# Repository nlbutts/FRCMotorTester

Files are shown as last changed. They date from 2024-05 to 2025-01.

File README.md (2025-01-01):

# Brushless Buddy
This is a small PCB with a display and two rotary encoders. The device
is designed to help teams quickly prototype BLC designs using the Rev SparkMax
motor controllers. Although it could be expanded to support other devices.

# Design
The block diagram is shown below. The design consists of an input buck regulator.
The regulator should be good up to 24V, but was designed to work at 12V. There
is reverse battery protection, so it should handle accidentially connecting
the battery up in reverse.

The buck generates 5V which is used for the CAN transceiver. The 5V is fed
to two LDO's to generate 3.3V for the processor and 3.0V for the LCD backlight.

There are two status LEDs on the board, two rotary encoders, and a 128x32 pixel
graphical LCD. An STM32F446 processor powers everything.

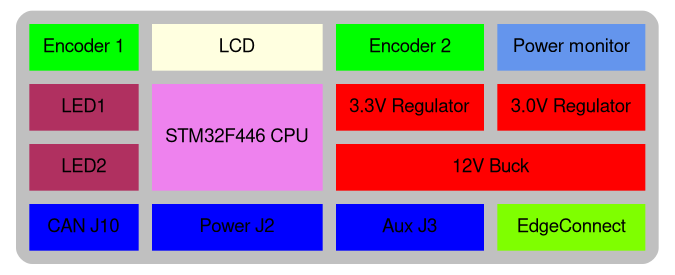
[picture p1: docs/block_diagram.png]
block diagram


There are three user accessible connectors:
Power J2:
| Pin | Use |
| -- | -- |
| 1 | Ground |
| 2 | Power |

The mate is a **JST PHR-2**

CAN J10:
| Pin | Use |
| -- | -- |
| 1 | CAN High |
| 2 | CAN Low |
| 3 | CAN High |
| 4 | CAN Low |

The pinout is the same as the Spark MAX and uses the same connector.
The mate is a **JST PHR-4**

Aux J3:
| Pin | Use |
| -- | -- |
| 1 | 3.3V |
| 2 | Ground |
| 3 | GPIO1 |
| 4 | GPIO2 |
| 5 | GPIO3 |
| 6 | Analog Input |

The mate is a **JST PHR-6**
The auxiliary connector is used for future use cases. It just made sense to
throw this connector on.

The picture below shows the location of the connectors.
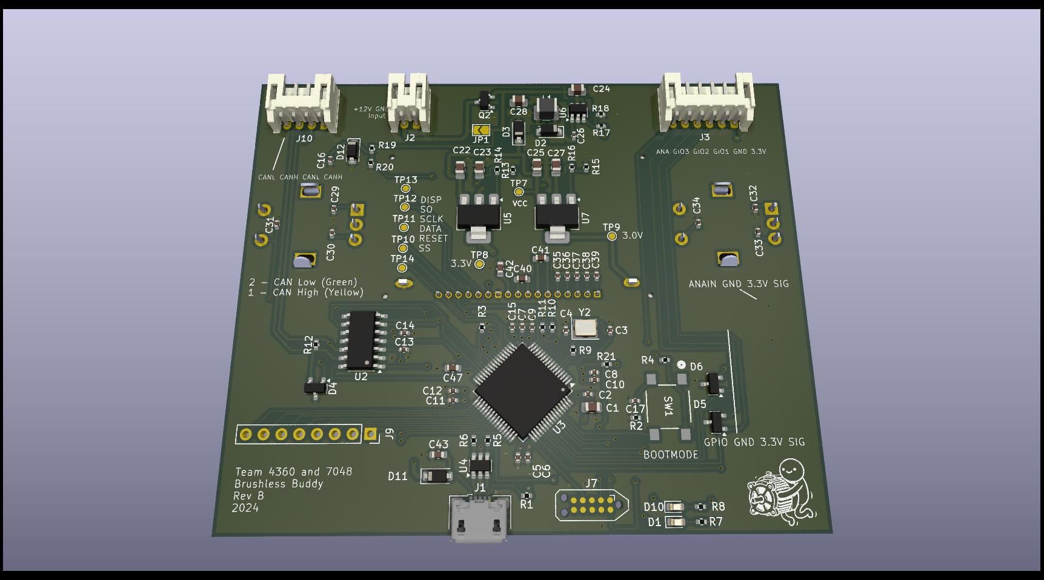
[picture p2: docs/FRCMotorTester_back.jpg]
connectors


# Software
The design runs Micropython. To re-build the code do the following:
1) Download the ARM GCC compiler [GCC](https://developer.arm.com/-/media/Files/downloads/gnu/13.3.rel1/binrel/arm-gnu-toolchain-13.3.rel1-x86_64-arm-none-eabi.tar.xz)
2) Decompress the toolchain to some known location, we will call this *<gcc_emd>*
3) Open a command prompt and update your path: `export PATH=<gcc_emd>/bin:$PATH`
4) Check out this repo, we will call this directory *<repo>*
5) Navigate to *<repo>/software/micropython
6) `make -C mpy-cross -j`
7) `BOARD=FRCMOTOR make -C ports/stm32/ -j`
8) Connect the Tagconnect to the board.
9) Program **firmware.elf** using the STM32CubeProgrammer.

## SWD Debug
It is assumed you are using a JLink and it is installed in **/opt/SEGGER/JLink**
In the software directory:
1) Run **gdbstart.sh** in one terminal
2) Run debug.sh in other terminal. You now have the full power of GDB at your literial finger tips

## Python

This device runs micropython. So the main program is a Python program. The
main program is called **main.py**, catchy aint it?

There are two levels of software upgrades. If you need to upgrade the Python code,
simply update main.py and copy it over to the **PYBFLASH** device.

If you need to update Micropython, then use a terminal program to open the REPL terminal.
Hit CTRL-C to stop the program. Then type
```
import machine
machine.bootloader()
```

This will put the processor in DFU upgrade mode. You can now use STM32CubeProgrammer to program
the DFU file. If the upgrade fails, then the device will have to be JTAGed. The next rev
of the PCB will fix a defect and a physical button will allow the unit to be booted in DFU mode.

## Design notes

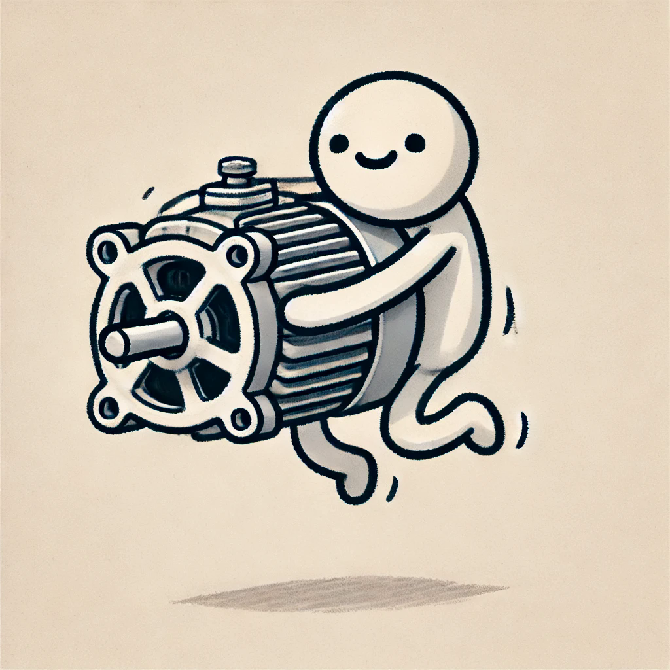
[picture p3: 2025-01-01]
brushless_buddy.png

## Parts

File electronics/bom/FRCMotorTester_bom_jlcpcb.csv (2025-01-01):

Designator | Comment | Footprint | JLCPCB
C1 | 4.7u | Capacitor_SMD:C_0805_2012Metric | C1779
C2 | 0.1u | Capacitor_SMD:C_0402_1005Metric | C1525
C3 | 15p | Capacitor_SMD:C_0402_1005Metric | C1548
C4 | 15p | Capacitor_SMD:C_0402_1005Metric | C1548
C5 | 0.1u | Capacitor_SMD:C_0402_1005Metric | C1525
C6 | 0.1u | Capacitor_SMD:C_0402_1005Metric | C1525
C7 | 0.1u | Capacitor_SMD:C_0402_1005Metric | C1525
C8 | 0.1u | Capacitor_SMD:C_0402_1005Metric | C1525
C9 | 0.1u | Capacitor_SMD:C_0402_1005Metric | C1525
C10 | 0.1u | Capacitor_SMD:C_0402_1005Metric | C1525
C11 | 0.1u | Capacitor_SMD:C_0402_1005Metric | C1525
C12 | 0.1u | Capacitor_SMD:C_0402_1005Metric | C1525
C13 | 0.1u | Capacitor_SMD:C_0402_1005Metric | C1525
C14 | 0.1u | Capacitor_SMD:C_0402_1005Metric | C1525
C15 | 1u | Capacitor_SMD:C_0402_1005Metric | C52923
C16 | 1u | Capacitor_SMD:C_0402_1005Metric | C52923
C17 | 0.1u | Capacitor_SMD:C_0402_1005Metric | C1525
C22 | 10u | Capacitor_SMD:C_0805_2012Metric | C15850
C23 | 10u | Capacitor_SMD:C_0805_2012Metric | C15850
C24 | 10u | Capacitor_SMD:C_0805_2012Metric | C15850
C25 | 10u | Capacitor_SMD:C_0805_2012Metric | C15850
C26 | 10n | Capacitor_SMD:C_0402_1005Metric | C15195
C27 | 10u | Capacitor_SMD:C_0805_2012Metric | C15850
C28 | 10u | Capacitor_SMD:C_0805_2012Metric | C15850
C29 | 10n | Capacitor_SMD:C_0402_1005Metric | C15195
C30 | 10n | Capacitor_SMD:C_0402_1005Metric | C15195
C31 | 0.1u | Capacitor_SMD:C_0402_1005Metric | C1525
C32 | 10n | Capacitor_SMD:C_0402_1005Metric | C15195
C33 | 10n | Capacitor_SMD:C_0402_1005Metric | C15195
C34 | 0.1u | Capacitor_SMD:C_0402_1005Metric | C1525
C35 | 1u | Capacitor_SMD:C_0402_1005Metric | C52923
C36 | 1u | Capacitor_SMD:C_0402_1005Metric | C52923
C37 | 1u | Capacitor_SMD:C_0402_1005Metric | C52923
C38 | 1u | Capacitor_SMD:C_0402_1005Metric | C52923
C39 | 1u | Capacitor_SMD:C_0402_1005Metric | C52923
C40 | 2.2u | Capacitor_SMD:C_0603_1608Metric | C23630
C41 | 2.2u | Capacitor_SMD:C_0603_1608Metric | C23630
C42 | 2.2u | Capacitor_SMD:C_0603_1608Metric | C23630
C43 | 2.2u | Capacitor_SMD:C_0603_1608Metric | C23630
C47 | 2.2u | Capacitor_SMD:C_0603_1608Metric | C23630
D1 | LED | LED_SMD:LED_0603_1608Metric | C2286
D2 | D_Schottky | Diode_SMD:D_SOD-123 | C8598
D3 | D_Schottky | Diode_SMD:D_SOD-123 | C8598
D4 | SP0502BAHT | Package_TO_SOT_SMD:SOT-23 | C32677
D5 | SP0502BAHT | Package_TO_SOT_SMD:SOT-23 | C32677
D6 | SP0502BAHT | Package_TO_SOT_SMD:SOT-23 | C32677
D10 | LED | LED_SMD:LED_0603_1608Metric | C2286
D11 | D_Schottky | Diode_SMD:D_SOD-123 | C8598
D12 | D_Zener | Diode_SMD:D_SOD-123 | C2105
DS1 | NHD-C12832A1Z-FSW-FBW-3V3 | footprints:LCD_NHD-C12832A1Z-FSW-FBW-3V3
J1 | USB_B_Micro | Connector_USB:USB_Micro-B_Amphenol_10118193-0001LF_Horizontal | C132562
J2 | Conn_01x02_Socket | Connector_JST:JST_PH_S2B-PH-K_1x02_P2.00mm_Horizontal | C173752
J3 | Conn_01x06 | Connector_JST:JST_PH_S6B-PH-K_1x06_P2.00mm_Horizontal | C471518
J10 | Conn_01x04 | Connector_JST:JST_PH_S4B-PH-K_1x04_P2.00mm_Horizontal | C160354
L1 | L | Inductor_SMD:L_1210_3225Metric | C1330201
Q2 | IRLML6401 | Package_TO_SOT_SMD:SOT-23 | C2593
R1 | 560 | Resistor_SMD:R_0402_1005Metric | C25126
R2 | 100k | Resistor_SMD:R_0402_1005Metric | C102750
R3 | 100k | Resistor_SMD:R_0402_1005Metric | C102750
R4 | 1K | Resistor_SMD:R_0402_1005Metric | C11702
R5 | 22 | Resistor_SMD:R_0402_1005Metric | C25152
R6 | 22 | Resistor_SMD:R_0402_1005Metric | C25152
R7 | 330 | Resistor_SMD:R_0402_1005Metric | C12246
R8 | 330 | Resistor_SMD:R_0402_1005Metric | C12246
R9 | 1K | Resistor_SMD:R_0402_1005Metric | C11702
R10 | 20k | Resistor_SMD:R_0402_1005Metric | C93942
R11 | 10k | Resistor_SMD:R_0402_1005Metric | C25744
R12 | 120 | Resistor_SMD:R_0402_1005Metric | C25079
R13 | 1.6k | Resistor_SMD:R_0402_1005Metric | C102825
R14 | 1k | Resistor_SMD:R_0402_1005Metric | C11702
R15 | 1.3k | Resistor_SMD:R_0402_1005Metric | C4906
R16 | 1k | Resistor_SMD:R_0402_1005Metric | C11702
R17 | 49.9k | Resistor_SMD:R_0402_1005Metric | C100457
R18 | 9.53k | Resistor_SMD:R_0402_1005Metric | C103191
R19 | 100k | Resistor_SMD:R_0402_1005Metric | C102750
R20 | 10k | Resistor_SMD:R_0402_1005Metric | C25744
R21 | 4.7k | Resistor_SMD:R_0402_1005Metric | C103059
SW1 | PTS645SK50SMTR92LFS | footprints:PTS645SK50SMTR92LFS_CNK | C221872
U2 | TCAN1043xDxQ1 | Package_SO:SOIC-14_3.9x8.7mm_P1.27mm | C1848115
U3 | STM32F446RETx | Package_QFP:LQFP-64_10x10mm_P0.5mm | C69336
U4 | USBLC6-2SC6 | Package_TO_SOT_SMD:SOT-23-6 | C7519
U5 | LM1117DT-ADJ | Package_TO_SOT_SMD:SOT-223-3_TabPin2 | C2902259
U6 | AOZ1280CI | Package_TO_SOT_SMD:SOT-23-6 | C41240
U7 | LM1117DT-ADJ | Package_TO_SOT_SMD:SOT-223-3_TabPin2 | C2902259
Y2 | Crystal_GND24 | Crystal:Crystal_SMD_3225-4Pin_3.2x2.5mm | C156247

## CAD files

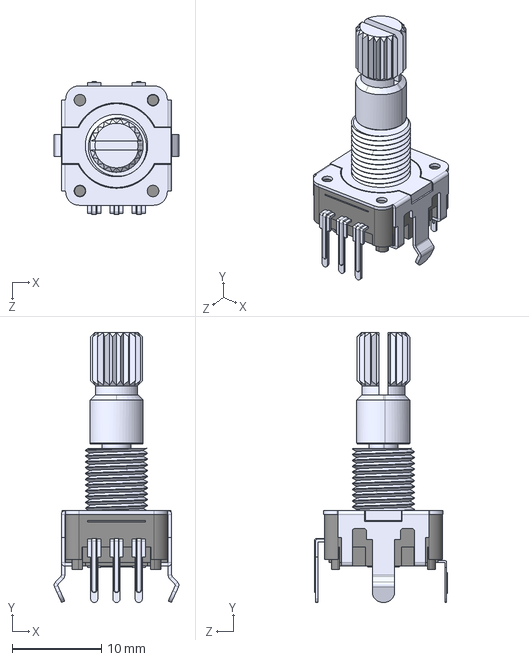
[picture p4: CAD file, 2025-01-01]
mechanical/PEC11R-4220K-S0024.STEP
14.0 x 30.3 x 14.9 mm

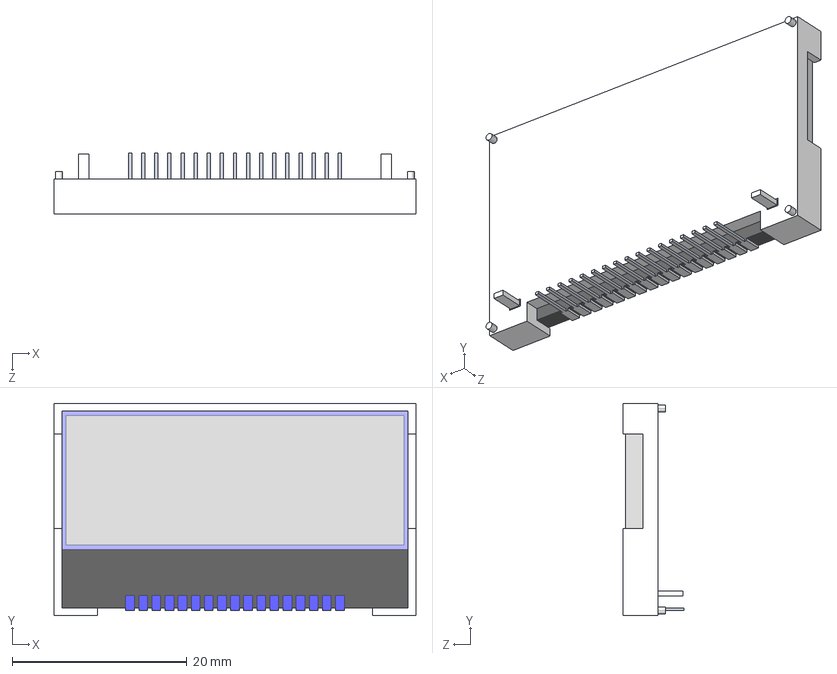
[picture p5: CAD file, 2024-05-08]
mechanical/NHD-C12832A1Z.STEP
41.4 x 24.3 x 7.00 mm

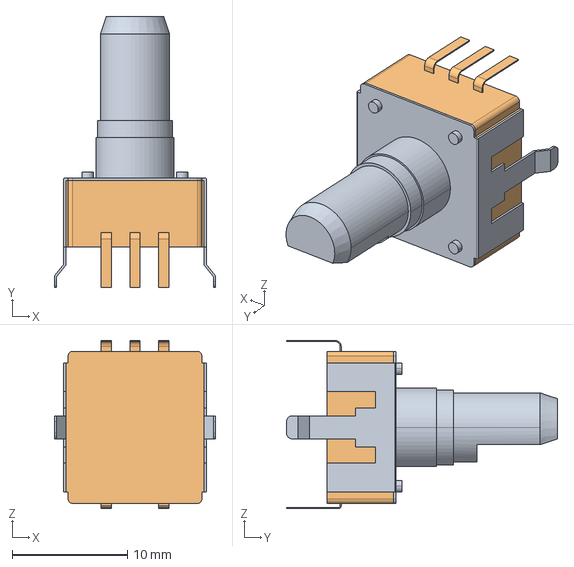
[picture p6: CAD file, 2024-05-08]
mechanical/en12-hs22af20.stp
14.0 x 23.5 x 14.6 mm
BM-427
BM-428

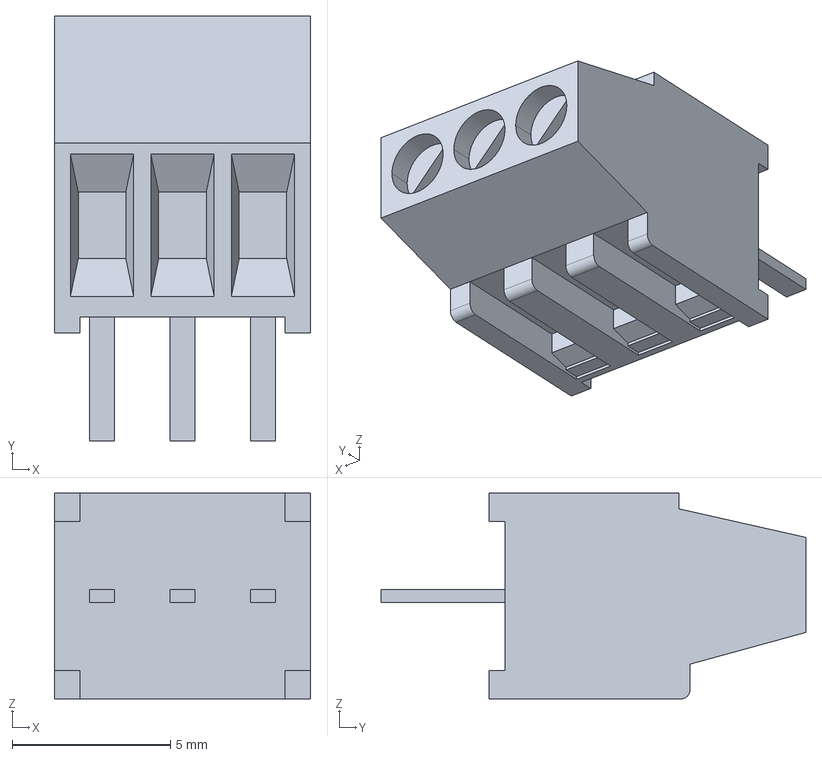
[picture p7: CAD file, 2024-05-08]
mechanical/c-282834-3-c-3d.stp
8.08 x 13.4 x 6.50 mm

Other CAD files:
mechanical/FRCMotorTester.step
mechanical/W25Q32JVZPIQ.step
mechanical/PTS645SK50SMTR92LFS.step
mechanical/LQH3NPN4R7MMEL.step
mechanical/CUI_DEVICES_TS04-66-65-BK-260-SMT.step
mechanical/CUI_DEVICES_TB002-500-02BE.step
mechanical/QFN28_6X6MC_MCH.step

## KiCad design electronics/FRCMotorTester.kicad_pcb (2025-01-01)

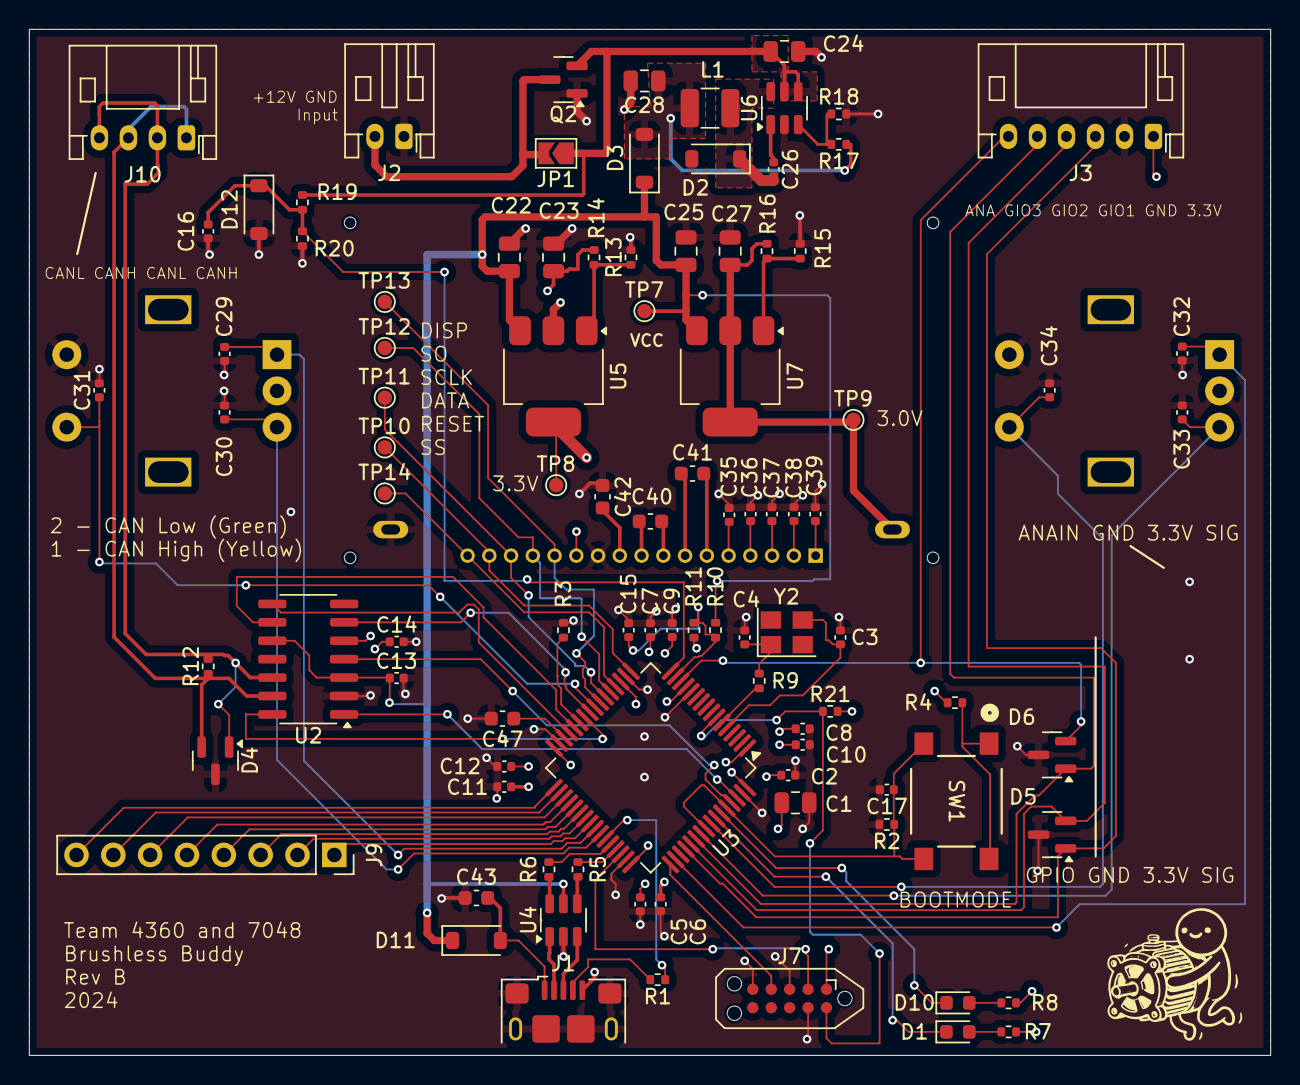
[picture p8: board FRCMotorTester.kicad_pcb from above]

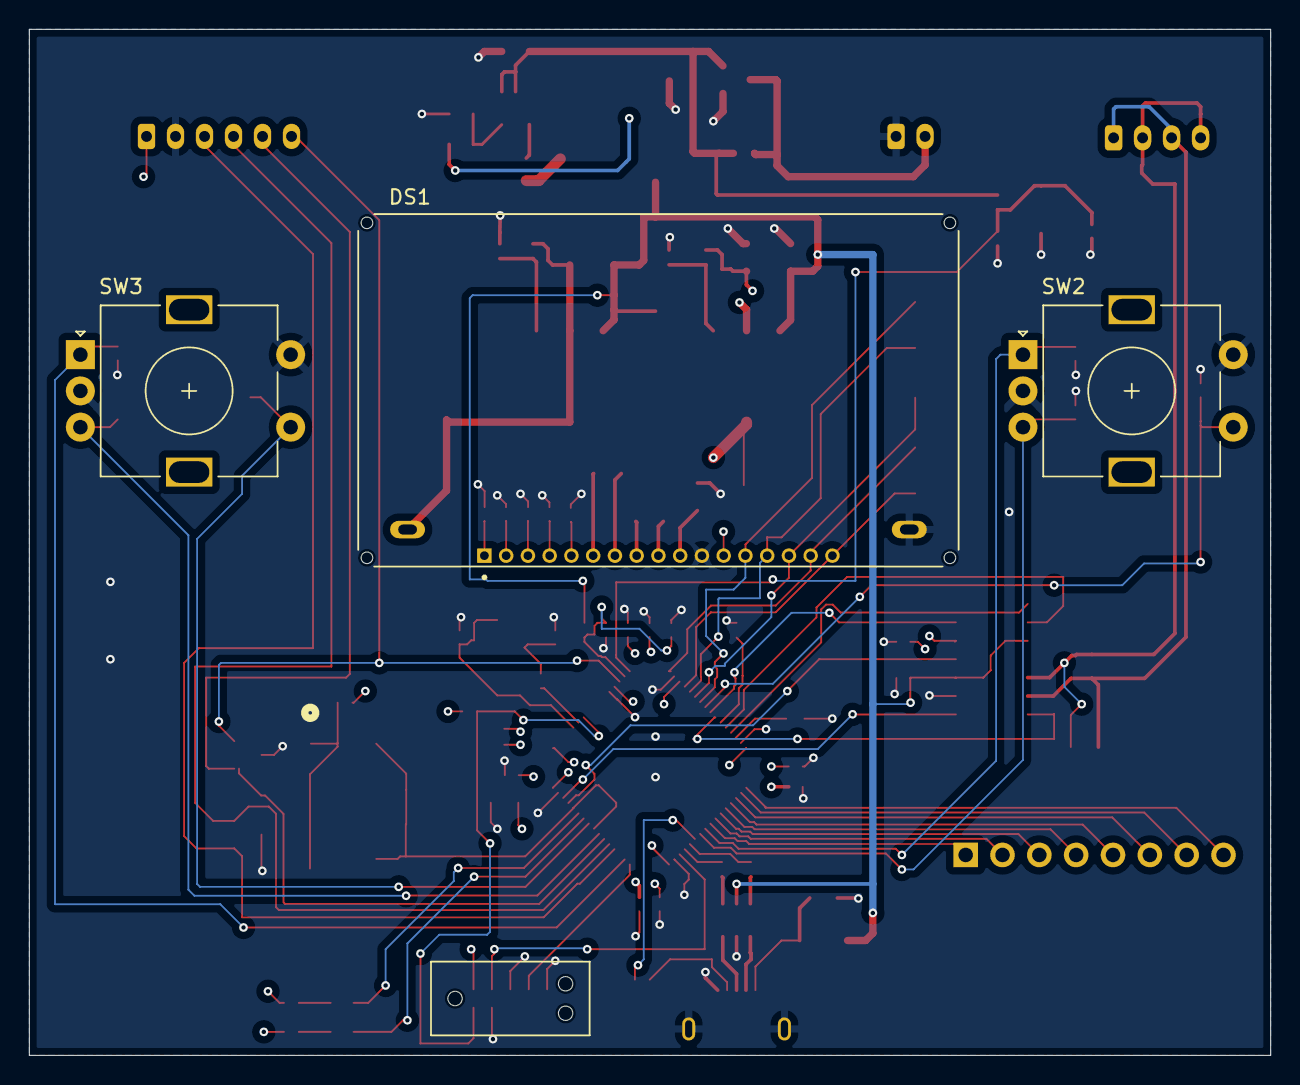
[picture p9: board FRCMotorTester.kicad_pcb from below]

Board: 4 copper layers, 85.6 x 70.8 mm, 99 parts (3 on the bottom side), 78 nets.

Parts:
C1: 4.7u; C_0805_2012Metric
C2, C5, C6, C7, C8, C9, C10, C11, C12, C13, C14, C17, C31, C34: 0.1u; C_0402_1005Metric
C3, C4: 15p; C_0402_1005Metric
C15, C16, C35, C36, C37, C38, C39: 1u; C_0402_1005Metric
C22, C23, C24, C25, C27, C28: 10u; C_0805_2012Metric
C26, C29, C30, C32, C33: 10n; C_0402_1005Metric
C40, C41, C42, C43, C47: 2.2u; C_0603_1608Metric
D1, D10: LED; LED_0603_1608Metric
D2, D3, D11: D_Schottky; D_SOD-123
D4, D5, D6: SP0502BAHT; SOT-23
D12: D_Zener; D_SOD-123
DS1: NHD-C12832A1Z-FSW-FBW-3V3; LCD_NHD-C12832A1Z-FSW-FBW-3V3
H1: MountingHole; brushless_buddy_logo
J1: USB_B_Micro; USB_Micro-B_Amphenol_10118193-0001LF_Horizontal
J2: Conn_01x02_Socket; JST_PH_S2B-PH-K_1x02_P2.00mm_Horizontal
J3: Conn_01x06; JST_PH_S6B-PH-K_1x06_P2.00mm_Horizontal
J7: Conn_ARM_JTAG_SWD_10; Tag-Connect_TC2050-IDC-NL_2x05_P1.27mm_Vertical_with_bottom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
J9: Conn_01x08; PinSocket_1x08_P2.54mm_Vertical
J10: Conn_01x04; JST_PH_S4B-PH-K_1x04_P2.00mm_Horizontal
JP1: Jumper_NO_Small; SolderJumper-2_P1.3mm_Open_TrianglePad1.0x1.5mm
L1: L; L_1210_3225Metric
Q2: IRLML6401; SOT-23
R1: 560; R_0402_1005Metric
R2, R3, R19: 100k; R_0402_1005Metric
R4, R9: 1K; R_0402_1005Metric
R5, R6: 22; R_0402_1005Metric
R7, R8: 330; R_0402_1005Metric
R10: 20k; R_0402_1005Metric
R11, R20: 10k; R_0402_1005Metric
R12: 120; R_0402_1005Metric
R13: 1.6k; R_0402_1005Metric
R14, R16: 1k; R_0402_1005Metric
R15: 1.3k; R_0402_1005Metric
R17: 49.9k; R_0402_1005Metric
R18: 9.53k; R_0402_1005Metric
R21: 4.7k; R_0402_1005Metric
SW1: PTS645SK50SMTR92LFS; PTS645SK50SMTR92LFS_CNK
SW2, SW3: RotaryEncoder_Switch; RotaryEncoder_Alps_EC11E-Switch_Vertical_H20mm
TP7, TP8, TP9, TP10, TP11, TP12, TP13, TP14: TestPoint; TestPoint_Pad_D1.0mm
U2: TCAN1043xDxQ1; SOIC-14_3.9x8.7mm_P1.27mm
U3: STM32F446RETx; LQFP-64_10x10mm_P0.5mm
U4: USBLC6-2SC6; SOT-23-6
U5, U7: LM1117DT-ADJ; SOT-223-3_TabPin2
U6: AOZ1280CI; SOT-23-6
Y2: Crystal_GND24; Crystal_SMD_3225-4Pin_3.2x2.5mm

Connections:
3V0: C27.1, DS1.A (LED+), R16.1, TP9.1, U7.2 (VO)
3V3: C1.1, C2.1, C5.1, C6.1, C7.1, C8.1, C9.1, C10.1, C11.1, C12.1, C14.1, C23.1, DS1.12 (VDD), J3.1, J7.1 (VTref), R4.1, R7.2, R8.2, R14.1, R21.2, TP8.1, U2.5 (VIO), U3.1 (VBAT), U3.13 (VDDA), U3.19 (VDD), U3.32 (VDD), U3.48 (VDD), U3.64 (VDD), U5.2 (VO)
+12V: C24.1, JP1.1, Q2.2 (S), R19.1, U6.4 (EN), U6.5 (VIN)
/Pico/OSC_IN: C3.2, U3.5 (PH0), Y2.3
/Pico/OSC_OUT: C4.2, R9.2, Y2.1
/Power/VIN: J2.2, JP1.2, Q2.3 (D)
ANALOG_IN: D6.2 (K), J3.6, U3.14 (PA0)
BOOT: C17.1, R2.1, SW1.3, SW1.4, U3.56 (PB4), U3.60 (BOOT0)
CAN_EN: U2.6 (EN), U3.25 (PC5)
CAN_FAULT: U2.8 (~FAULT), U3.29 (PB10)
CAN_RX: U2.4 (RXD), U3.61 (PB8)
CAN_STB: U2.14 (~STB), U3.26 (PB0)
CAN_TX: U2.1 (TXD), U3.62 (PB9)
CAN_WAKE: U2.9 (WAKE), U3.28 (PB2)
DISP_DATA: DS1.15 (A0), TP11.1, U3.22 (PA6)
DISP_RESET: DS1.16 (~RST), TP10.1, U3.17 (PA3)
DISP_SCLK: DS1.14 (SCL), TP12.1, U3.21 (PA5)
DISP_SI: DS1.13 (SI), TP13.1, U3.23 (PA7)
DISP_SS: DS1.17 (~CS1), TP14.1, U3.20 (PA4)
DM: R6.2, U3.44 (PA11)
DP: R5.2, U3.45 (PA12)
ENC1A: C29.1, SW2.A, U3.41 (PA8)
ENC1B: C30.1, SW2.B, U3.42 (PA9)
ENC2A: C32.1, SW3.A, U3.50 (PA15)
ENC2B: C33.1, SW3.B, U3.55 (PB3)
GENIO_01: D5.1 (K), J3.3, U3.52 (PC11)
GENIO_02: D5.2 (K), J3.4, U3.53 (PC12)
GENIO_03: D6.1 (K), J3.5, U3.54 (PD2)
GND: C1.2, C2.2, C3.1, C4.1, C5.2, C6.2, C7.2, C8.2, C9.2, C10.2, C11.2, C12.2, C13.2, C14.2, C15.2, C16.2, C17.2, C22.2, C23.2, C24.2, C25.2, C27.2, C28.2, C29.2, C30.2, C31.2, C32.2, C33.2, C34.2, C35.1, C36.1, C37.1, C38.1, C39.1, C42.1, C43.1, C47.2, D2.2 (A), D4.3 (A), D5.3 (A), D6.3 (A), D12.2 (A), DS1.11 (VSS), DS1.K (LED-), J1.5 (GND), J1.6 (Shield), J2.1, J3.2, J7.3 (GND), J7.5 (GND), J7.9 (GNDDetect), Q2.1 (G), R2.2, R3.2, R11.2, R13.2, R15.2, R18.2, R20.2, SW2.C, SW2.S2, SW3.C, SW3.S2, U2.2 (GND), U3.12 (VSSA), U3.18 (VSS), U3.31 (VSS), U3.47 (VSS), U3.63 (VSS), U4.2 (GND), U6.2 (GND)
ID: R1.1, U3.43 (PA10)
LED1: D1.1 (K), U3.58 (PB6)
LED2: D10.1 (K), U3.59 (PB7)
NRST: J7.10 (~RESET), R21.1, U3.7 (NRST)
unnamed: D1.2 (A), R7.1
unnamed: C26.2, D2.1 (K), L1.1, U6.6 (LX)
unnamed: C28.1, D3.2 (A), L1.2, R17.1
unnamed: D10.2 (A), R8.1
unnamed: C43.2, D11.2 (A), J1.1 (VBUS)
unnamed: C40.1, DS1.8 (C1+)
unnamed: C40.2, DS1.9 (C1-)
unnamed: C41.1, DS1.7 (C2+)
unnamed: C41.2, DS1.6 (C2-)
unnamed: C39.2, DS1.1 (V0)
unnamed: C38.2, DS1.2 (V1)
unnamed: C37.2, DS1.3 (V2)
unnamed: C36.2, DS1.4 (V3)
unnamed: C35.2, DS1.5 (V4)
unnamed: C42.2, DS1.10 (VOUT)
unnamed: J1.3 (D+), U4.3 (I/O2)
unnamed: J1.2 (D-), U4.1 (I/O1)
unnamed: J1.4 (ID), R1.2
unnamed: D4.2 (K), J10.1, J10.3, R12.1, U2.13 (CANH)
unnamed: D4.1 (K), J10.2, J10.4, R12.2, U2.12 (CANL)
unnamed: R4.2, SW1.1, SW1.2
unnamed: R5.1, U4.4 (I/O2)
unnamed: R6.1, U4.6 (I/O1)
unnamed: R3.1, U3.27 (PB1)
unnamed: R9.1, U3.6 (PH1)
unnamed: C47.1, U3.30 (VCAP_1)
unnamed: R13.1, R14.2, U5.1 (ADJ)
unnamed: C26.1, U6.1 (BST)
unnamed: R17.2, R18.1, U6.3 (FB)
unnamed: R15.1, R16.2, U7.1 (ADJ)
PRESS1: C31.1, SW2.S1, U3.24 (PC4)
PRESS2: C34.1, SW3.S1, U3.57 (PB5)
SPARE1: J9.1, U3.40 (PC9)
SPARE2: J9.2, U3.39 (PC8)
SPARE3: J9.3, U3.38 (PC7)
SPARE4: J9.4, U3.37 (PC6)
SPARE5: J9.5, U3.36 (PB15)
SPARE6: J9.6, U3.35 (PB14)
SPARE7: J9.7, U3.34 (PB13)
SPARE8: J9.8, U3.33 (PB12)
SWCLK: J7.4 (SWCLK/TCK), U3.49 (PA14)
SWDIO: J7.2 (SWDIO/TMS), U3.46 (PA13)
VCC: C13.1, C22.1, C25.1, D3.1 (K), D11.1 (K), R10.1, TP7.1, U2.3 (VCC), U2.10 (VSUP), U4.5 (VBUS), U5.3 (VI), U7.3 (VI)
VCC_MEAS: C15.1, R10.2, R11.1, U3.15 (PA1)
VIN_MEAS: C16.1, D12.1 (K), R19.2, R20.1, U3.16 (PA2)

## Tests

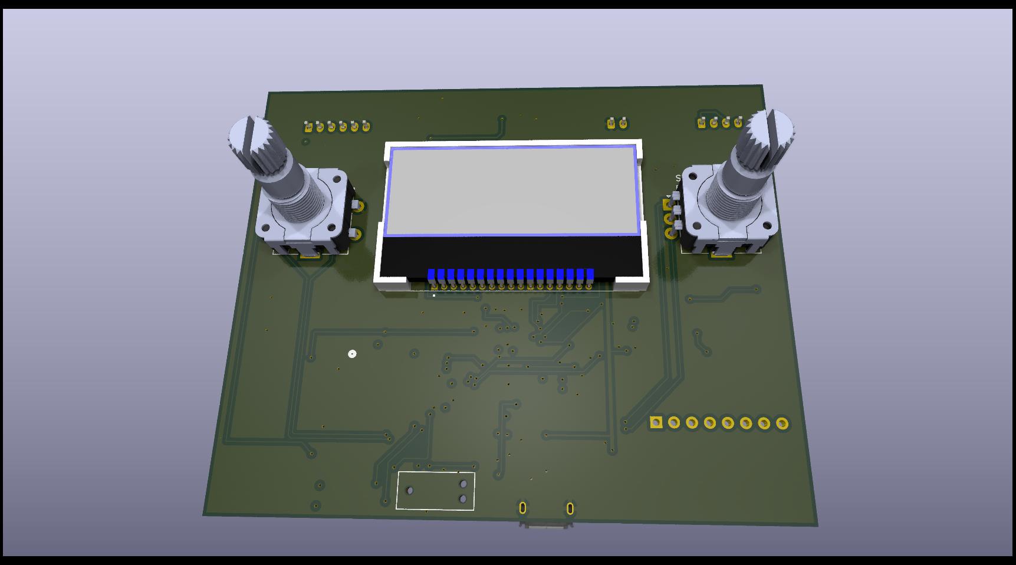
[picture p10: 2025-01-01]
docs/FRCMotorTester_front.jpg

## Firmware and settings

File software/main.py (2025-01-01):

from machine import Pin
from pyb import CAN
import pyb
import time
import sys
import struct

VERSION = 1.0

class SparkMax():
    def __init__(self, can, id, enc):
        self.can = can
        self.id = id
        self.enc = enc
        self.prev_button = 1
        self.arm = False
        self.volts = 0
        self.current = 0
        self.motor_output = 0.0
        self.enc.set_counter(0)

    def make_filter(self, class_idx):
        """Make a message filter

        Args:
            class_idx (int): combination of the API class and index
        """
        devtype = 2
        mfg = 5
        can_id = devtype << 24 | mfg << 16 | class_idx << 6 | self.id
        return can_id

    def process_button(self):
        button = self.enc.get_press()
        if not button and self.prev_button:
            self.arm = not self.arm
            if not self.arm:
                self.enc.set_counter(0)

        self.prev_button = button

    def process(self, msg):
        self.process_button()

        can_id = msg[0]
        dev = can_id & 0x3F
        api = (can_id >> 6) & 0x3FF
        if dev == self.id:
            if api == 0x61:
                data = msg[4]
                volts = ((data[6] & 0x0F) << 8) | data[5]
                self.volts = volts / 128.0
                current = data[7] << 4 | (data[6] >> 4) & 0xF
                self.current = current / 20

        if self.enc.get_counter() > 100:
            self.enc.set_counter(100)
        elif self.enc.get_counter() < -100:
            self.enc.set_counter(-100)
        self.motor_output = -(self.enc.get_counter())
        self.motor_output /= 100
        self.drive_motor(self.motor_output)

    def get_arm_str(self):
        if self.arm:
            return 'ARMD'
        return 'SAFE'

    def get_info(self):
        info = {}
        info['id'] = self.id
        info['arm'] = self.get_arm_str()
        info['volt'] = self.volts
        info['current'] = self.current
        info['output'] = self.motor_output
        return info

    def drive_motor(self, output):
        """
        Driving motor 2 uses this message: DevID: 0 idx: 2 cls: 11 mfg: 5 devtype: 2 raw: 02052C80 data: 04 00 00 00 00 00 00 00
        At -0.12 DevID: 2 idx: 2 cls: 0 mfg: 5 devtype: 2 raw: 02050082 data: 8F C2 F5 BD 00 00 00 00
        Driving motor 4 uses this message: DevID: 0 idx: 2 cls: 11 mfg: 5 devtype: 2 raw: 02052C80 data: 10 00 00 00 00 00 00 00
        """
        if self.arm:
            devtype = 2
            mfg = 5
            cls = 0
            idx = 2
            can_id = devtype << 24 | mfg << 16 | cls << 10 | idx << 6 | self.id
            data = struct.pack('<fBBBB', output, 0, 0, 0, 0)  # Format the payload
            self.can.send(data, can_id, extframe=True)  # Send the CAN message

    def debug_can(self, message):
        """Debug the can message

        Args:
            message (_type_): _description_
        """
        id = message[0]
        devtype = id >> 24
        mfg = (id >> 16) & 0xFF
        cls = (id >> 10) & 0x3F
        idx = (id >> 6) & 0xF
        devid = id & 0x3F
        s = f'DevID: {devid} idx: {idx} cls: {cls} mfg: {mfg} devtype: {devtype} raw: {id:08X} data: '
        for b in message[4]:
            s += f'{b:02X} '
        print(s)

def get_spark_max_ids(can, delay=2):
    try:
        ids = {}
        start = time.time()
        while time.time() - start < delay:
            m = can.recv(0)
            id = m[0] & 0x3F
            if id > 0:
                ids[id] = 1
        print(ids)
        return list(ids.keys())
    except:
        return []

class Encoder():
    def __init__(self, enc_name):
        if 'Left' in enc_name:
            self.pin_a = Pin('ENC2A', Pin.AF_PP, pull=Pin.PULL_UP, af=Pin.AF1_TIM2)
            self.pin_b = Pin('ENC2B', Pin.AF_PP, pull=Pin.PULL_UP, af=Pin.AF1_TIM2)
            self.press = Pin('PRESS2', Pin.IN, pull=Pin.PULL_UP)
            self.tim = pyb.Timer(2, prescaler=0, period=100)
            self.ch = self.tim.channel(1, pyb.Timer.ENC_AB)
        elif 'Right' in enc_name:
            self.pin_a = Pin('ENC1A', Pin.AF_PP, pull=Pin.PULL_UP, af=Pin.AF1_TIM1)
            self.pin_b = Pin('ENC1B', Pin.AF_PP, pull=Pin.PULL_UP, af=Pin.AF1_TIM1)
            self.press = Pin('PRESS1', Pin.IN, pull=Pin.PULL_UP)
            self.tim = pyb.Timer(1, prescaler=0, period=100)
            self.ch = self.tim.channel(1, pyb.Timer.ENC_AB)

    def get_press(self):
        return self.press.value()

    def get_counter(self):
        return self.tim.counter() - 500

    def set_counter(self, value):
        self.tim.counter(500 + value)

sw = Pin('SW', Pin.IN)
prev = sw.value()

lcd = pyb.LCD('X')

can_txd = Pin('CAN_TX', Pin.AF_PP, af=Pin.AF9_CAN1)
can_rxd = Pin('CAN_RX', Pin.AF_PP, af=Pin.AF9_CAN1)

can_en = Pin('CAN_EN', Pin.OUT)
can_fault = Pin('CAN_FAULT', Pin.IN)
can_wake = Pin('CAN_WAKE', Pin.OUT)
can_stb = Pin('CAN_STB', Pin.OUT)

can_en.value(1)
can_fault.value(1)
can_wake.value(1)
can_stb.value(1)

# Initialize CAN bus
can = CAN(1, CAN.NORMAL)

# Configure the CAN bus settings
can.init(CAN.NORMAL, prescaler=2, sjw=1, bs1=14, bs2=6, auto_restart=True)
can.setfilter(0, can.MASK32, 0, (0, 0), extframe=True)
can.send('hello', 0, extframe=True)

leftEnc = Encoder('Left')
rightEnc = Encoder('Right')

def show_boot_screen(can_ids=[]):
    lcd.fill(0)
    lcd.text(f'Brushless Buddy', 0, 0, 1)
    lcd.text(f'Ver: {VERSION}', 0, 10, 1)
    if len(can_ids) > 0:
        s = 'Found: '
        for id in can_ids:
            s += f'{id} '
        lcd.text(s, 0, 20, 1)
    else:
        lcd.text(f'Found: None', 0, 20, 1)
    lcd.show()

show_boot_screen()
ids = sorted(get_spark_max_ids(can))
print(f'Found ids: {ids}')

if len(ids) > 2:
    lcd.fill(0)
    lcd.text('Too many CAN', 0, 0, 1)
    lcd.text('nodes on bus', 0, 10, 1)
    lcd.show()
    time.sleep(5)
    sys.reset()
if len(ids) == 0:
    lcd.fill(0)
    lcd.text('No SparkMaxs', 0, 0, 1)
    lcd.text('detected', 0, 10, 1)
    lcd.text('rebooting', 0, 20, 1)
    lcd.show()
    time.sleep(5)
    machine.reset()

motors = []
if len(ids) == 1:
    motors.append(SparkMax(can, ids[0], leftEnc))
elif len(ids) == 2:
    motors.append(SparkMax(can, ids[0], leftEnc))
    motors.append(SparkMax(can, ids[1], rightEnc))

#debug_can(can, 0)

start = time.time()
while True:
    msg = can.recv(0)
    motor_info = []
    arm_field = 0
    for motor in motors:
        motor.process(msg)
        motor_info.append(motor.get_info())
        if motor.arm:
            arm_field |= 1 << motor.id

    # Send the heartbeat message
    can_id = 0x02052C80
    data = struct.pack('<II', arm_field, 0)
    can.send(data, can_id, extframe=True, timeout=100)

    if time.time() - start > 0.1:
        start = time.time()
        lcd.fill(0)
        if len(motor_info) == 1:
            lcd.text(f'{motor_info[0]['id']}/{motor_info[0]['arm']}', 0, 0, 1)
            lcd.text(f'{motor_info[0]['output']}', 0, 10, 1)
            lcd.text(f'{motor_info[0]['volt']:.1f}/{motor_info[0]['current']}', 0, 20, 1)
        else:
            str = f'{motor_info[0]['id']}/{motor_info[0]['arm']} | {motor_info[1]['arm']}/{motor_info[1]['id']}'
            lcd.text(str, 0, 0, 1)

            str = f'{motor_info[0]['output']:5.2f}  | {motor_info[1]['output']:5.2f}'
            lcd.text(str, 0, 10, 1)

            str = f'{motor_info[0]['volt']:.1f}V/ {motor_info[0]['current']:2.1f} / {motor_info[1]['current']:2.1f}'
            lcd.text(str, 0, 20, 1)
        lcd.show()

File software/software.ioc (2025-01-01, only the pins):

Mcu.UserName=STM32F446RETx
PA0-WKUP.Signal=ADCx_IN0
PA1.Signal=ADCx_IN1
PA10.GPIO_Label=ID
PA10.Signal=GPIO_Input
PA11.Signal=USB_OTG_FS_DM
PA12.Signal=USB_OTG_FS_DP
PA13.Signal=SYS_JTMS-SWDIO
PA14.Signal=SYS_JTCK-SWCLK
PA15.GPIO_Label=ENC2A
PA15.Signal=S_TIM2_CH1_ETR
PA2.Signal=ADCx_IN2
PA3.GPIO_Label=DISP_RESET
PA3.Signal=GPIO_Output
PA4.Signal=SPI1_NSS
PA5.Signal=SPI1_SCK
PA6.GPIO_Label=DISP_DATA
PA6.Signal=GPIO_Output
PA7.Signal=SPI1_MOSI
PA8.GPIO_Label=ENC1A
PA8.Signal=S_TIM1_CH1
PA9.GPIO_Label=ENC1B
PA9.Signal=S_TIM1_CH2
PB0.GPIO_Label=CAN_STB
PB0.Signal=GPIO_Output
PB10.GPIO_Label=CAN_FAULT
PB10.Signal=GPIO_Input
PB2.GPIO_Label=CAN_WAKE
PB2.Signal=GPIO_Output
PB3.GPIO_Label=ENC2B
PB3.Signal=S_TIM2_CH2
PB4.GPIO_Label=SW
PB4.Signal=GPIO_Input
PB5.GPIO_Label=PRESS2
PB5.Signal=GPIO_Input
PB6.GPIO_Label=LED1
PB6.Signal=GPIO_Output
PB7.GPIO_Label=LED2
PB7.Signal=GPIO_Output
PB8.Signal=CAN1_RX
PB9.Signal=CAN1_TX
PC11.GPIO_Label=GENIO1
PC11.Signal=GPIO_Input
PC12.GPIO_Label=GENIO2
PC12.Signal=GPIO_Input
PC4.GPIO_Label=PRESS1
PC4.Signal=GPIO_Input
PC5.GPIO_Label=CAN_EN
PC5.Signal=GPIO_Output
PC6.GPIO_Label=SPARE4
PC6.Signal=GPIO_Input
PC7.GPIO_Label=SPARE3
PC7.Signal=GPIO_Input
PC8.GPIO_Label=SPARE2
PC8.Signal=GPIO_Input
PC9.GPIO_Label=SPARE1
PC9.Signal=GPIO_Input
PD2.GPIO_Label=GENIO3
PD2.Signal=GPIO_Input
PH0-OSC_IN.Signal=RCC_OSC_IN
PH1-OSC_OUT.Signal=RCC_OSC_OUT

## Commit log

2024-02-26 Initial checkin.
    [Can.kicad_sch, FRCMotorTester.kicad_pcb, FRCMotorTester.kicad_sch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]
2024-05-08 Many changes to the design. Fully routed.
    [CUI_DEVICES_TB002-500-02BE.step, CUI_DEVICES_TS04-66-65-BK-260-SMT.step, Can.kicad_sch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]
2024-05-20 Almost sent this to fab. It is getting expensive.
    [Can.kicad_sch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]
2024-08-04 Switched processor.
    [Can.kicad_sch, FRCMotorTester.kicad_pcb, Pico.kicad_sch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]
2024-08-04 Ordered this version.
    [Can.kicad_sch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]
2024-08-12 Tweaked parts to use Basic parts which are cheaper.
    [Can.kicad_sch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]
2024-08-14 Updated parts based on request from JLCPCB.
    [FRCMotorTester_bom.csv, Pico.kicad_sch]
2024-10-20 Made some changes and thought I should check it in.
    [IO.kicad_sch, Pico.kicad_sch]
2024-11-24 Updated design for REV B.
    [Can.kicad_sch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]
2024-12-27 This version is working well. Need to figure out USB DFU programming.
    [Can.kicad_sch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]
